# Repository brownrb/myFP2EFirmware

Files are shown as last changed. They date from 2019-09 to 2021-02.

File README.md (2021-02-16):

# myFP2ESP Firmware for ESP32 and ESP8266 myFP2ESP Controllers
This is the firmware for the myFocuserPro2E ESP8266 and ESP32 focus controller projects on Sourceforge.

(c) Robert Brown and Holger Manz, 2019-2021. All rights reserved.

The source code is located in the **src** folder. 

#APPLICATIONS
The Windows applications are found on Sourceforge.  
https://sourceforge.net/projects/myfocuserpro2-esp32/files/Windows%20Application/  

The Linux application and source code is found on Sourceforge.  
https://sourceforge.net/projects/myfocuserpro2-esp32/files/Linux%20Application/  

The ASCOM drivers are found on Sourceforge.  
https://sourceforge.net/projects/myfocuserpro2-esp32/files/ASCOM%20Drivers/  

# FIRMWARE
The firmware is found on GitHub. Download as a zip file then extract the zip file to access the library files and firmware.  
https://github.com/brownrb/myFP2EFirmware/releases

# PCB GERBER FILES  
The Gerbers files for the PCB are found on Sourceforge.  
https://sourceforge.net/projects/myfocuserpro2-esp32/files/PCB%20Gerber%20Files/  

# PDF
To get a clear understanding of myFP2ESP features and options, it is essential to read the PDF.  
https://sourceforge.net/projects/myfocuserpro2-esp32/files/Documentation/  

# Compiling for ESP8266
Compiling the source code requires Arduino IDE **v1.8.13** with the ExpressIF ESP8266 Arduino extensions.
You will need to add the JSON file for the ESP8266 library by using the File->Preferences menu of the 
Arduino IDE and add the location for the library into the board manager
http://arduino.esp8266.com/stable/package_esp8266com_index.json

Once specified, open the board manager, scroll down to ESP8266 and install version **v2.7.4**.
Then you can specify the target board as **Node MCU v1.0 (ESP-12E)** with Flash Size set to 4M (1MB SPIFFS) and upload speed of 115200.

Note: Additional JSON files are separated in board manager by using a comma ,

# Compiling for ESP32
Compiling the source code requires Arduino IDE **v1.8.13** with the ExpressIF ESP32 Arduino extensions.
You will need to add the JSON file for the ESP32 library by using the File->Preferences menu of the 
Arduino IDE and add the location for the library into the board manager
https://dl.espressif.com/dl/package_esp32_index.json  

Once specified, open the board manager, scroll down to ESP32 and install the latest version
Then you can specify the target board as **ESP32 Dev** with Flash Size set t 4M (1MB SPIFFS) and upload speed of 115200.

### Note1:  
Additional JSON files are separated in board manager by using a comma ,  
### Note2:  
When installed the folder C:\Program Files (x86)\Arduino\libraries\WiFi prevents compiling of ESP8266 firmware so move the WIFI folder to C:\Program Files (x86)\Arduino\libraries.old\WiFi  

# Additional JSON library Needed
Make sure you install the library ArduinoJson into the Arduino IDE else firmware will not compile.
The latest version is at https://github.com/bblanchon/ArduinoJson/releases  

# Libraries
To compile you will also need to import these libraries in the folder src/myFP2ELibs into the Arduino IDE environment using the Menu - Sketch - Include Library - Add .Zip file

* myOLED
* myHalfStepperESP32
* myDallasTemperature
* myfp2eIRremoteESP8266

Do not edit or replace any of these library files with others.

# Additional Libraries which must be downloaded and installed
To compile this firmware you need to ensure that you have installed a number of "library" files into the Arduino environment. For each of the links below, you need to DOWNLOAD the ZIP file first.

OneWire
https://github.com/PaulStoffregen/OneWire  

IRRemote
https://github.com/crankyoldgit/IRremoteESP8266  

DuckDNS
https://github.com/ayushsharma82/EasyDDNS  

ESP32 Sketch Data uploader
https://github.com/me-no-dev/arduino-esp32fs-plugin/releases/  

ESP8266 Sketch Data uploader
https://github.com/esp8266/arduino-esp8266fs-plugin  

After downloading the zip files, you then need to install these into the Arduino IDE environment. To do that, start the Arduino IDE, select Sketch, Include Library, Add .Zip library, then navigate to where the ZIP files are stored and select them (you can only load 1 zip file at a time so please repeat this for all ZIP files).

The Sketch Data uploaders require a different method for installing. The install instructions are found in their respective download pages and require copying the files into a special folder of the Arduino program installation.

Once you have done this, you can start programming the controller.

# Hardware Driver Boards
One firmware file supports all driver boards [a different file supports the L293D motor shield driver board for the ESP8266]. The user must set the **DRVBRD** at the beginning of the firmware file [myBoards.h] to the correct driver board, eg, #define DRVBRD PRO2EULN2003 will set the driver board to an ULN2003 using an ESP8266 chip.

# focuserconfig.h
Configuration information about the controller is specified in the *focuserconfig.h* file. This is where you specify the controller options like OLEDTEXT and HOMEPOSITIONSWITCH, as well as the controller mode such as ACCESSPOINT or STATIONMODE.

# Controller Modes
The controller supports the modes ACCESSPOINT, STATIONMODE, LOCALSERIAL for ESP8266 with an additional BLUETOOTHMODE for the ESP32.

# Command Process Handler Routine
At present a single command process handler manages received commands for LOCALSERIAL, BLUETOOTH [ESP32 only] of TCP/IP. This must handle each controller mode, so some variables had to be made global to do this.

# FocuserSetupData.cpp and .h files
At present these must be in the same folder as the .ino file, but will later migrate to a library. These files handle the SPIFFS data, saving, restoring and persistance of controller settings. A JSON file in file system SPIFFS area is used to store focuser data.

# myBoards.cpp and .h files
This implements a driver board class for the supported driver boards [DRV8825, ULN2003, L298N, L293DMINI, L9110S]. There is one constructor for this class which accepts the boardtype, the user should never have to change the main code within the firmware file which sets up the driver boards. All pins mappings for the controller chip, hardware options and the driver board are specified here. DO NOT MODIFY THESE FILES.

# generalDefinitions.h
This file contains general definitions for all controllers, such as motor speed, step modes, focuser limits etc.

# ESPQueue.h
This file manages the Bluetooth serial data for ESP32 chips. It is a modified version of the Queue.h file from Steven de Salas. DO NOT MODIFY THIS FILE. It has been modified to work with ESP8266 and ESP32 chips.

# HalfStepperESP32 Library
This library manages the stepping modes for the ULN2003, L298N, L293DMINI and L9110S driver boards. It is a modified version of the HalfStepper library from Tom Biuso. DO NOT MODIFY THESE FILES. It has been modified to work with ESP8266 and ESP32 chips.

# myOLED Libary
This is a special cut down version of the SSD1306AsciiWire library by Bill Greiman. The library has been reduced in size and a number of additional features added. DO NOT MODIFY THESE FILES.

# COMPILE ENVIRONMENT : Tested with 

* Arduino IDE 1.8.13
* ESP8266 Arduino Core 2.7.4

Libraries 

* Arduino JSON 6.15.2 https://github.com/bblanchon/ArduinoJson.git  
* myfp2eIremoteESP8266 as in Library Files
* myOLED as in Library Files
* myHalfStepperESP32 as in Library Files
* myDallas Temperature as in Library Files
* Wire [as installed with Arduino 1.8.13]
* OneWire http://www.pjrc.com/teensy/td_libs_OneWire.html  

# Notes:
You may need to turn 12V off to reprogram chip. Speed is 115200. Sometimes you might need to
remove the chip from PCB before re-programming new firmware. Remember to remove WIFI library
as instructed in PDF when programming ESP32.

# ESP8266 ISSUES
One chip I have boots fine.
Another chip will not boot properly from 12V only. I need to plug in USB cable, press reset 
then turn on 12V for it to boot correctly. ESP8266 Arduino lib 2.2.0 does not work with this 
chip either.

# TODO
Look at what need to be when chip starts up, do we need a delay reset circuit?

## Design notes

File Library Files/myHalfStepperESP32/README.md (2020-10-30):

# myFP2E Firmware for ESP32 and ESP8266
This is the firmware for the myFocuserPro2E ESP8266 and ESP32 focus controller projecta on Sourceforge.
https://sourceforge.net/projects/arduinoascomfocuserpro2diy/files/myFocuserPro2E/
https://sourceforge.net/projects/myfocuserpro2-esp32/

(c) Robert Brown, 2019. All rights reserved.
(c) Holger Manz, 2019. All rights reserved.

The source code is located in the src folder. 

#HalfStepperESP32.h and HalfStepperESP32.cpp
This file manages the stepping modes for the ULN2003, L298N, L293DMINI and L9110S driver boards. It is a modified version of the HalfStepper library from Tom Biuso. DO NOT MODIFY THESE FILES. It has been modified to work with ESP8266 and ESP32 chips.

# HalfStepper

#### An Arduino library to enable half-stepping and single/dual phasing for step motors.
---

HalfStepper decorates (wraps) the Stepper library to provide half-step states and has options for single/dual phasing as well as multiple coil sequencing options.
<br/>
<br/>This library is able to drive motors directly or through drivers with motor control or H-bridge chips, such as the L293, L298, and L9110.

---

## License
Copyright � 2016 Tom Biuso.
<br />This library is released under the GNU Lesser General Public License v3.0.
<br />See LICENSE file for detailed terms and LGPL v3.0 license text.
<br />
<br />Based upon the Stepper Arduino library.
<br />Copyright � Arduino LLC, Sebastian Gassner, Noah Shibley.
<br />Also released under the GNU LGPL.

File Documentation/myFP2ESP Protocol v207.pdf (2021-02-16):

1 | P a g e

## myFP2ESP Comms Protocol

© Robert Brown, 2014-2021. All Rights Reserved. © Holger Manz, 2019-2021. All Rights Reserved. myFP2™, myFP2ESP8266™, myFP2ESP32™ v207 (17-February-2021)
Applicable to Firmware version 144+

### GENERAL PRINCIPLES

// Command Protocol, commands to controller begin with : and end with #
// responses from controller begin with Char, then response and end with #
// the char response indicates what command requested the response, ie. P = Get focuser Position

// Not all commands return responses

### COMPATIBILITY WITH MYFOCUSERPRO2 IN LOCALSERIALMODE

In general, when configured as LOCALSERIAL, myFP2 applications and drivers should be able to be control the myFP2ESP controller.

### INDI

In general, the myFP2ESP controller will work with the existing INDI driver for myFP2 either in Serial USB or TCP/IP modes.

2 | P a g e

### COMMANDS [TCP/IP OR SERIAL OR BLUETOOTH]

:00# | Pxxxx# | Get current focuser position
:01# | Ixx# | Get motor moving status - 1 if moving, 0 otherwise
:02# | EOK# | Get motor controller status - Controller Response to "Are we connected"
:03# | F204# | Get Controller firmware version string (Fxxx#)
:04# | FString# | Get firmware version string (Fprogram name, version, #)
:05xxxxxx# | None | Set new target position to XXXXXX
| | (and focuser initiates immediate move to XXXXXX)
:06# | Zxxxxxx# | Get temperature as a float xx.xx
:07xxxxxx# | None | Set MaxStep between 1000 and 2000000
:08# | Mxxxxxx# | Get MaxStep, returns Long Integer XXXXXX
:09# | | Not used
:10# | Yxxxxxx# | Get MaxIncrement, returns maxsteps value XXXXXX
:11# | Oxx# | Get Coil Power setting
| | (0 = coils released after move, 1 = coil pwr on after move)
:12xx# | None | Set Coil Power 0=release pwr after move, 1=keep power on after move
:13# | Rxx# | Get Reverse Direction setting, 0 off, 1 on
:14xx# | None | Set Reverse Direction setting 0=normal, 1=reversed
:15xx# | None | Set Motor speed, 0 = Slow, 1 = Med, 2 = Fast
:16# | None | Display in Celsius (LCD or TFT)
:17# | None | Display in Fahrenheit (LCD or TFT)
:180# | None | Set the return of user specified stepsize to be OFF - default
:181# | None | Set the return of user specified stepsize to be ON
:19xxxx# | None | Set the step size value - double type, eg 2.1 (0.001-50.0)
:20xx# | None | Set the temperature resolution setting for DS18B20 temperature probe
:21# | Qxx# | Get temperature probe resolution setting (9, 10, 11 or 12)
:22xxx# | None | Set the temperature coefficient value to xxx
:23x# | None | Set the temperature compensation ON (1) or OFF (0)
:24# | 1xx# | Get state of Temperature Compensation, 0=disabled, 1=enabled
:25# | Ax# | Get if Temperature Compensation available 0=No, 1=Yes
:26# | Bxxx# | Get Temperature Coefficient (in steps per degree)
:27# | None | Stop a move - like a Halt
:28# | None | Home the motor to position 0
:29# | Sxx# | Get stepmode, returns XX
:30xx# | None | Set stepmode
(1=Full, 2=Half, 4=1/4, 8=1/8, 16=1/16, 32=1/32, 64=1/64, 128=1/128, 256=1/256)
:31xxxxxx# | None | Set current motor position to XXXXXX
| | (does not move, updates currentpos and targetpos to XXXXXX)
:32# | Ux# | Get if Stepsize is enabled in controller (true or false, 0/1)
:33# | Txxxxx# | Get step size in microns (if enabled by controller)
:34# | Xxxxxx# | Get the time that an LCD screen is displayed for
| | (in milliseconds, eg 2 = 2seconds
:35xxxx# | None | Set length of time an LCD page is displayed for in seconds 2-10s
:360# | None | Disable Display
:361# | None | Enable Display
:37# | Dxx# | Get Display status 0=disabled, 1=enabled
:38# | b# | Get Temperature Mode, Celsius=1, Fahrenheit=0
:39# | Nxxxxxx# | Get the new motor position (target) XXXXXX (not used yet)
:40# | None | Reboot controller
:41# | String# | Troubleshooting only

3 | P a g e
:42# | None | Reset focuser defaults
:43# | Cx# | Get motorspeed (0=slow, 1=medium, 2=fast)
:44xxx# | None | RETIRED from firmware 292 onwards
| | (set motorspeed threshold when moving)
:45# | Gxxx# | RETIRED from firmware 292 onwards (get TSWTHRESHOLD - 200)
:46x# | None | RETIRED from firmware 292 onwards
| | (set enable/disable motorspeed change when moving)
:47# | Jx# | RETIRED from firmware 292 onwards
| | (get state of motorspeedchange, enabled/disabled)
:48# | None | Save settings in SPIFFS
:49# | aString# | Get authenticated firmware MD5 Hash
:50# | lx# | Get if Home Position Switch enabled in firmware, 0 = no, 1 = yes
:51# | dipaddr# | Get ESP-WiFiController IP Address
:52# | enum# | Get ESP-WiFiController number of TCP packets sent
:53# | fnum# | Get ESP-WiFiController number of TCP packets received
:54# | gstr# | Get ESP-WiFiController SSID
:55# | 0xxxx# | Get motor speed delay (for current speed setting)
:56xxxx# | None | Set motor speed delay (for current speed setting)
:57# | None | Set Super Slow Jogging Speed [0 or 1]
:58# | mxxxx# | get Features [now redundant]
:59# | | Unused
:60xx# | None | Set MotorSpeed when jogging
:61xx# | None | Set update of position on lcd when moving (0=disable, 1=enable)
:62# | Lxx# | Get update of position on lcd when moving (0=disable, 1=enable)
:63# | Hxx# | Get status of home position switch (0=off, 1=closed, position 0)
:64xxx# | None | Move a specified number of steps (relative mode + or -)
:65x# | None | Set jogging state enable/disable
:66# | Kxx | Get jogging state enabled/disabled
:67x# | None | Set jogging direction, 0=IN, 1=OUT
:68# | Vx# | Get jogging direction, 0=IN, 1=OUT
:69# | None | RETIRED (sets EEPROMWRITES to 0)
:70# | Wxxxxxx# | RETIRED (gets number of EEPROMWrites so far, Nano up to 10,000)
:71xxx# | None | Set DelayAfterMove
:72# | 3xxx# | Get DelayAfterMove
:730# | None | Disable backlash IN (going to lower focuser position)
:731# | None | Enable backlash IN
:74# | 4x# | Get backlash IN enabled status [0 or 1]
:750# | None | Disable backlash OUT (going to higher focuser position)
:751# | None | Enable backlash OUT
:76# | 5x# | Get backlash OUT enabled status [0 or 1]
:77xx# | None | Set backlash steps IN
:78# | 6xx# | Get number of backlash steps IN
:79xx# | None | Set backlash steps OUT
:80# | 7xx# | Get number of backlash steps OUT
:81# | 8xxx# | Get number of backlash maximum steps
:82xxx# | None | Set backlash maximum steps
:83# | cx# | Get if there is a temperature probe, 0 = No, 1 = Yes
:84# | None | Set Nextion Page
:85xxx# | None | Set Serial Port Speed [Nextion only], xxx=9600, 19200, 38400, 57600
:86# | jxxxx# | Get Serial Port Speed [Nextion only]
:87# | kx# | Get Temperature compensation direction (1=IN, 0 =OUT)

4 | P a g e
:88x# | None | Set Temperature compensation direction (1=IN, 0 =OUT)
:89x# | 9x# | Get stepper power [myFP2]
:90xyyyy# | None | Set preset x [0-9] with position value yyyy [unsigned long]
:91x# | hyyyyy# | Get preset number x [0-9] [as unsigned long]
:92xxx# | None | Set OLED page display option
:93# | lxxx# | Get OLED page display option
:94x# | | Set DelayedDisplayUpdate (0=disabled, 1-enabled)
:95# | nx# | Get DelayedDisplayUpdate (0=disabled, 1-enabled)
:96x# | None | Set management options
| | (ASCOM server=1, in-out leds=2, temp probe=4, webserver=8)
:97# | mx# | Get management options
| | (ASCOM server=1, in-out leds=2, temp probe=4, webserver=8)
:98# | sx# | Get Network Signal Strength RSSI
:99x# | | Set Home Position Switch state [0=disabled, 1-enabled]

RETURNED VALUES BEGIN WITH A CHAR, FOLLOWED BY A VALUE (AS A STRING) AND TERMINATED WITH A HASH #

5 | P a g e

### MANAGEMENT SERVER [PORT 6060]

FILE MANAGEMENT
/delete | Delete a SPIFFS file
/list | List all SPIFFS files
/upload | Upload a file to SPIFFS

ASCOM REMOTE ALPACA SERVER
/ascomoff
/ascomon

IN-OUT LED’s
/ledsoff
/ledson

TEMPERATURE PROBE
/tempon
/tempoff

WEB-SERVER
/webserveroff
/webserveron

CONTROLLER OPTIONS
/halt | Halt the focuser motor [if moving]
/reboot | Reboot the myFP2ESP controller

NETWORK OPTIONS
/rssi | Return Network Signal Strength

6 | P a g e

### JSON CALLS

/set? | Set specific service or value
/set?ascom=off | Stop the ASCOM Alpaca remote server
/set?ascom=on | Start the ASCOM Alpaca remote server
/set?coilpower=off | Disable Coil power
/set?coilpower=on | Enable Coil power
/set?display=off | Disable the OLED display
/set?display=on | Enable the OLED display
/set?hpsw=off | Disable Home Position Switch
/set?hpsw=on | Enable Home Position Switch
/set?leds=off | Disable the IN-OUT LED’s
/set?leds=on | Enable the IN-OUT LED’s
/set?motorspeed=0 | Set Motor speed [0=slow, 1=medium, 2=fast]
/set?move=4192 | Move the focuser to position 4192
/set?position=5000 | Set focuser position to 5000 [Not a move]
/set?reverse=off | Set Reverse Direction off
/set?reverse=on | Set Reverse Direction on
/set?tempprobe=on | Enable the temperature probe [if fitted]
/set?tempprobe=off | Disable the temperature probe [if fitted]
/set?webserver=off | Stop the web-server
/set?webserver=on | Start the web-server
/get? | Get specific service or value
/get?ascom= | Return state of ASCOM Alpaca Remote Server [0 = off/disabled,
1=on/enabled]
/get?coilpower= | Return state of Coil power
/get?display= | Return state of display
/get?leds= | Return state of IN-OUT LED’s
/get?hpsw= | Return state of Home Position Switch [0=disabled, 1=enabled]
/get?ismoving= | Return if focuser is moving
/get?motorspeed= | Return motorspeed [0=slow, 1=medium, 2=fast]
/get?position= | Return the focuser position
/get?reverse= | Return reverse direction [0 = off/disabled, 1=on/enabled]
/get?tempprobe= | Return state of temperature probe
/get?webserver= | Return state of web-server
/get?rssi= | Return network strength

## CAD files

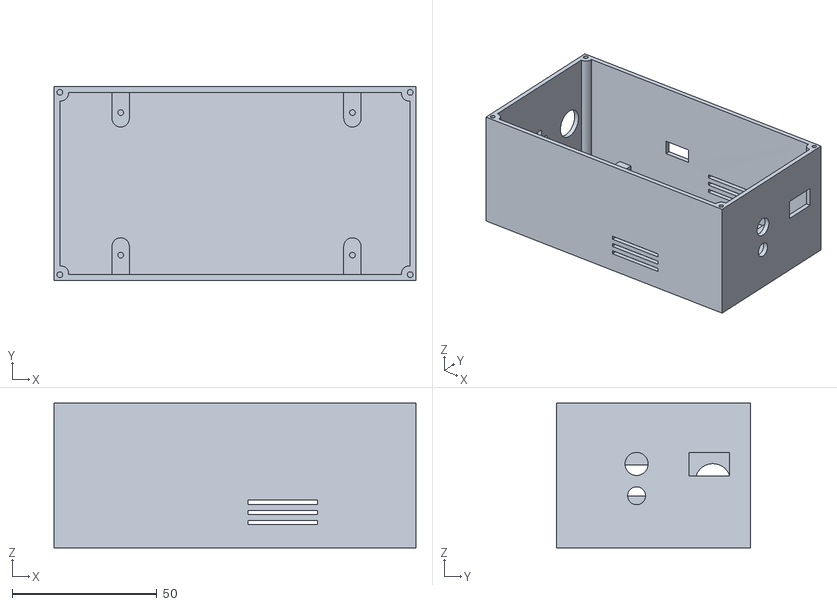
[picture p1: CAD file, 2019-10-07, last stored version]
3D Printed Cases/ESP32/DRV8825/Case-ESP32-DRV-PB-OLED-00.stl
125.0 x 67.0 x 50.0

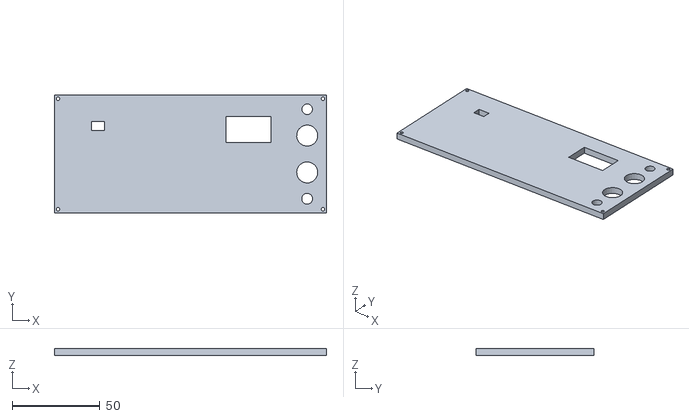
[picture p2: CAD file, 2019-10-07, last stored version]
3D Printed Cases/ESP32/ULN2003/Lid-ESP32-ULN-PB-OLED-IR-00.stl
155.0 x 67.0 x 4.00

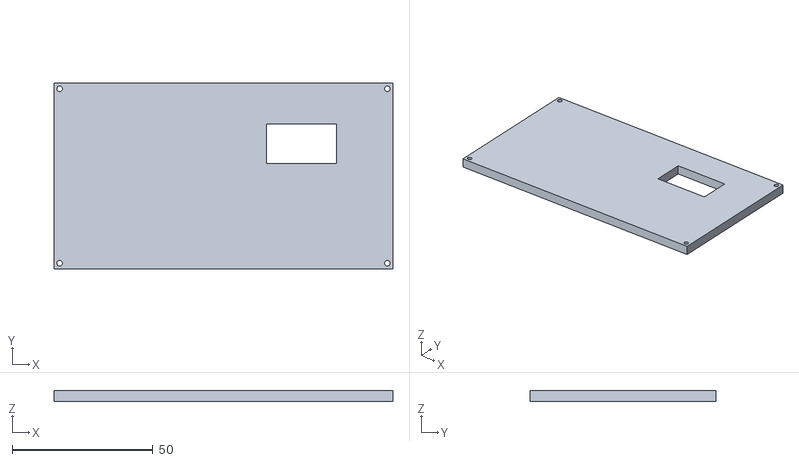
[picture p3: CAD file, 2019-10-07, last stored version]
3D Printed Cases/ESP8266/DRV8825-Big Chip/Lid-OLED-B-DRV-NoHoles-00.stl
120.5 x 66.0 x 4.00

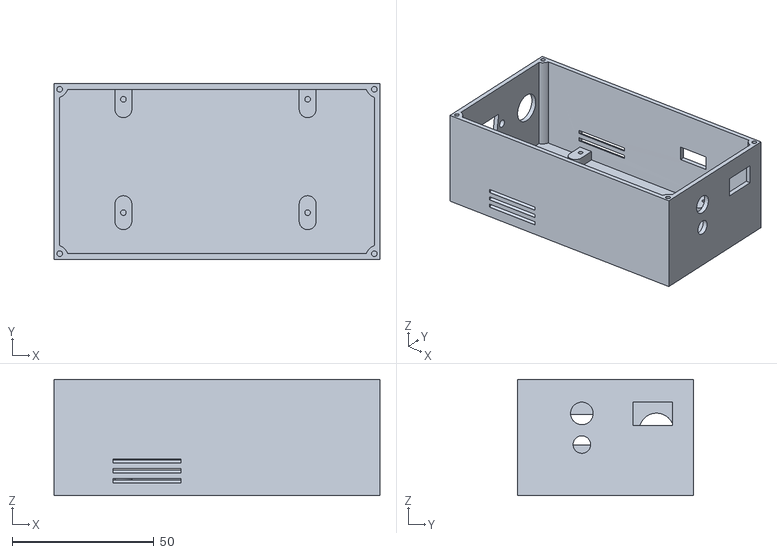
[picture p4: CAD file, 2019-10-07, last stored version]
3D Printed Cases/ESP8266/DRV8825/Case-S-DRV-00.stl
115.0 x 62.0 x 41.0

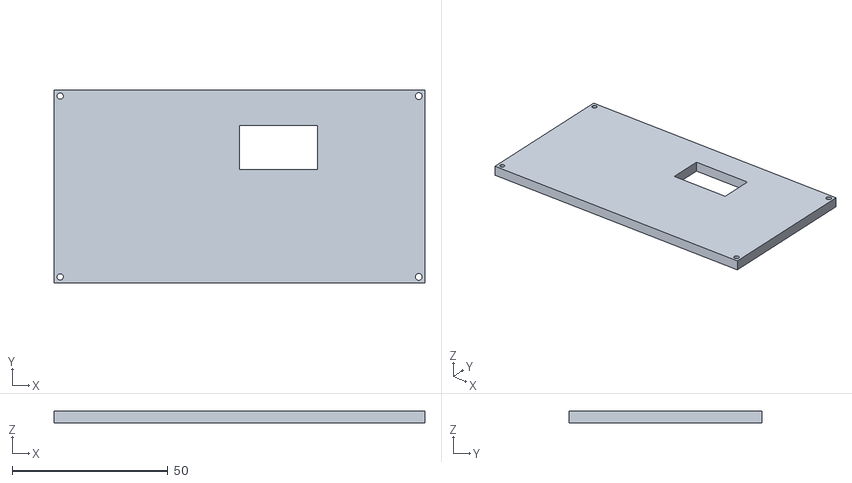
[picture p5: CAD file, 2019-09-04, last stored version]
3D Printed Cases/ESP8266/L293D Motor Shield/Lid-OLED-L293D-Shield-NoHoles-00.stl
119.0 x 62.0 x 4.00

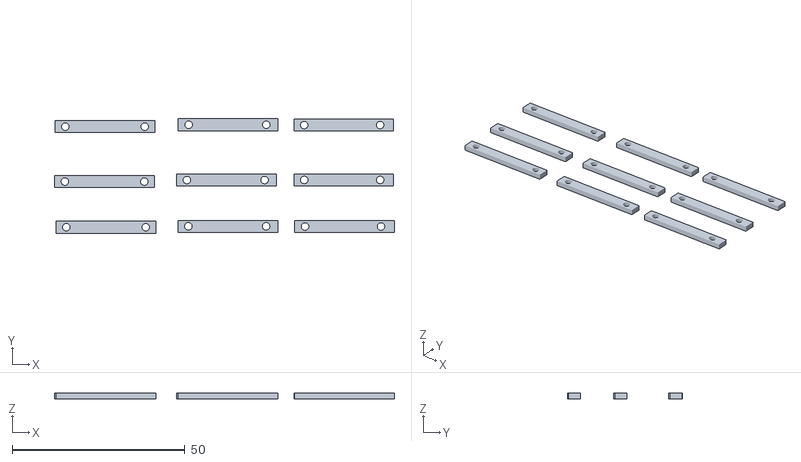
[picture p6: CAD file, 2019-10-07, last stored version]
3D Printed Cases/ESP8266/Lid OLED Little Spacer/lid-oled-support-22-23mm.stl
98.5 x 33.2 x 1.60

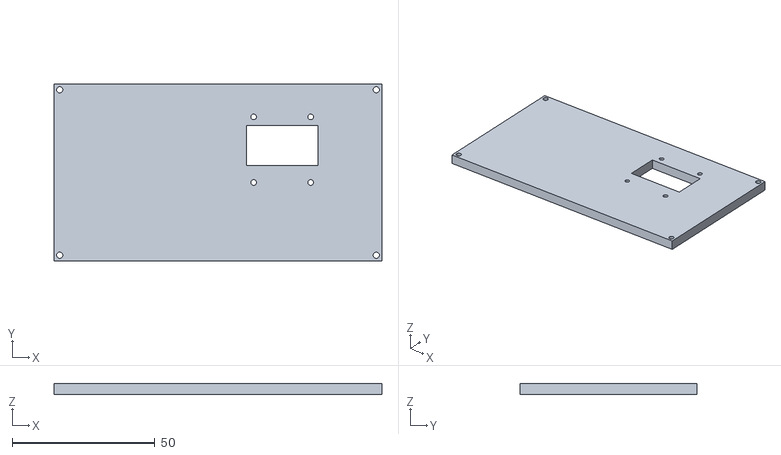
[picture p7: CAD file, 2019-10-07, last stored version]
3D Printed Cases/ESP8266/Lid-OLED-Shenglongsi-00.stl
115.0 x 62.0 x 4.00

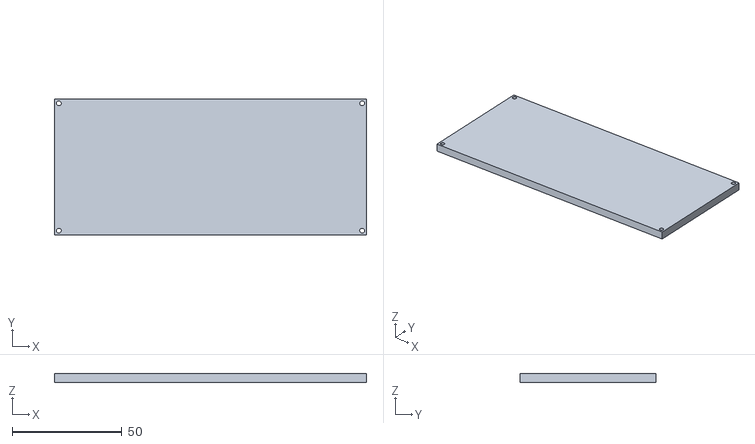
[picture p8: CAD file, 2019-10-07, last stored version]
3D Printed Cases/ESP8266/ULN2003-L298N/Lid-ULN-L298N-NOLED-00.stl
142.0 x 62.0 x 4.00

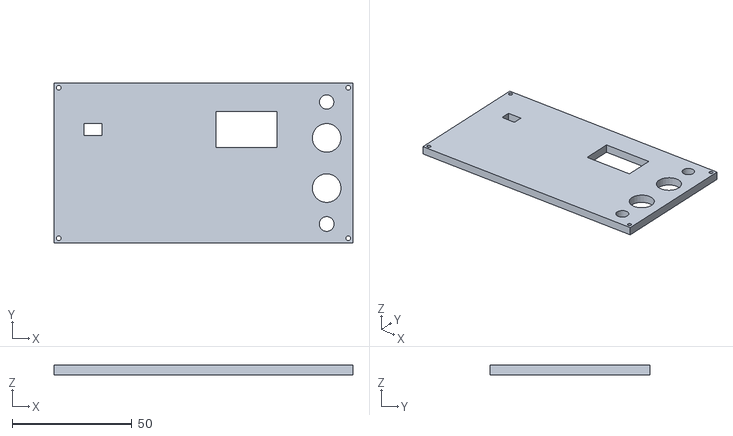
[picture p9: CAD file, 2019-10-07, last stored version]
3D Printed Cases/ESP32/DRV8825/Lid-ESP32-DRV-PB-OLED-IR-00.stl
125.0 x 67.0 x 4.00

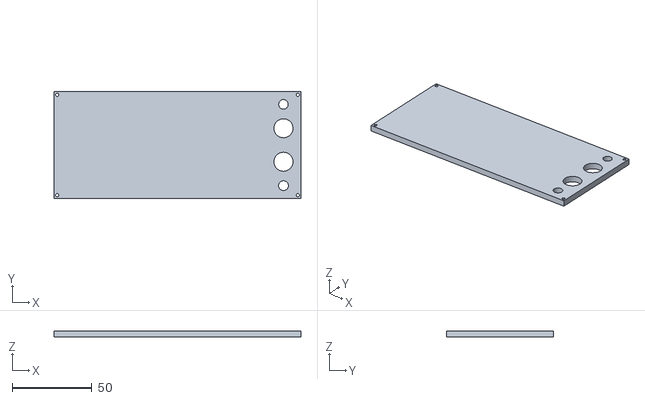
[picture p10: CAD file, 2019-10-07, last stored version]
3D Printed Cases/ESP32/ULN2003/Lid-ESP32-ULN-PB-00.stl
155.0 x 67.0 x 4.00

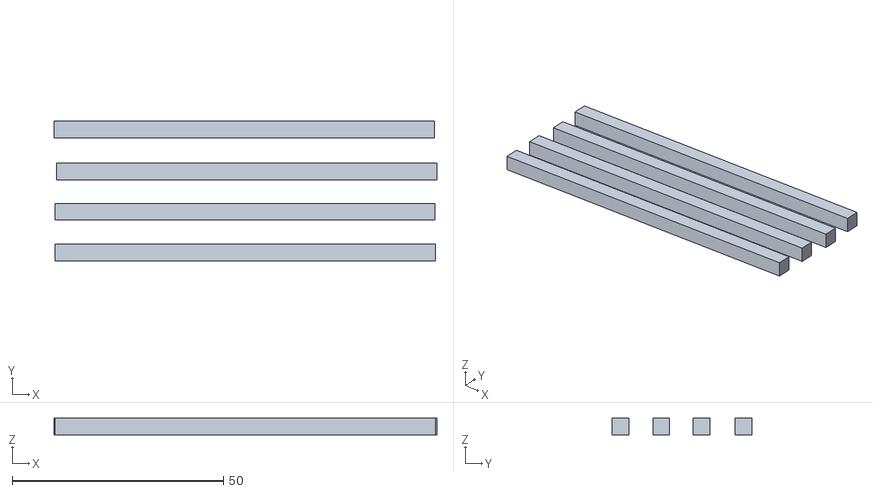
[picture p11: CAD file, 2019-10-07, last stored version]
3D Printed Cases/ESP8266/Bracing for E-oled lid.stl
90.6 x 33.1 x 4.00

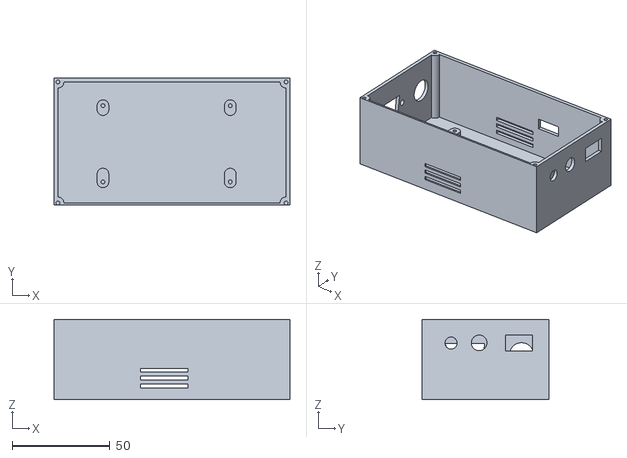
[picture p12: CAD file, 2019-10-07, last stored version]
3D Printed Cases/ESP8266/DRV8825-Big Chip/Case-B-DRV-00.stl
120.5 x 64.8 x 41.0

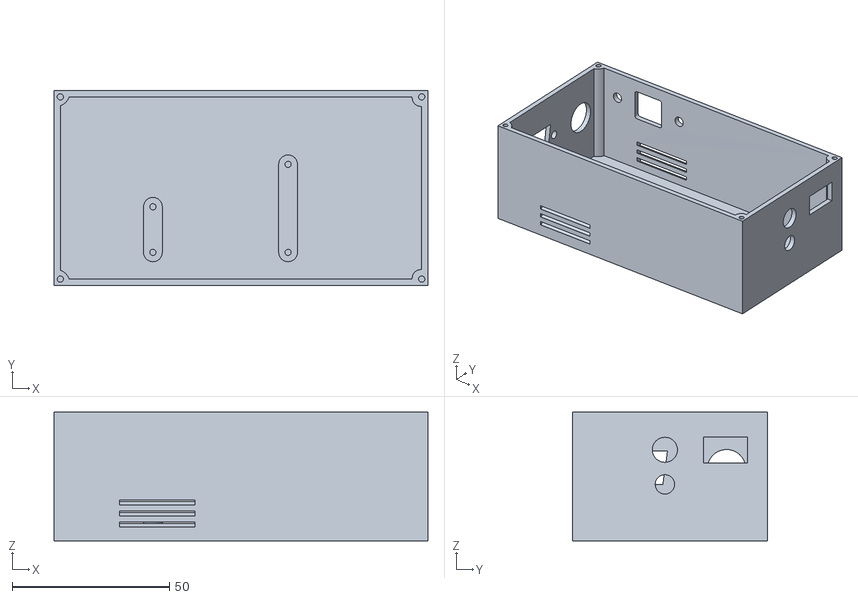
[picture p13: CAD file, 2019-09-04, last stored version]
3D Printed Cases/ESP8266/L293D Motor Shield/Case-L293D-Shield-00.stl
119.0 x 62.0 x 41.0

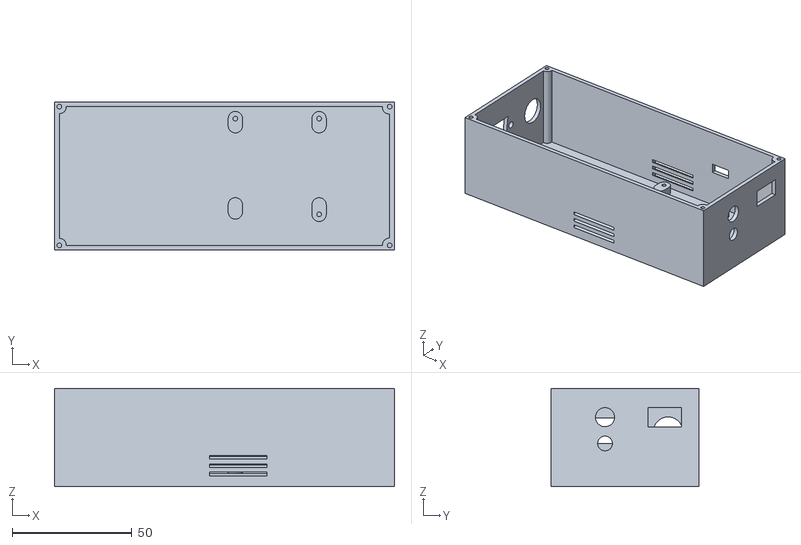
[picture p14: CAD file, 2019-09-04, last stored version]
3D Printed Cases/ESP8266/ULN2003-L298N/Case-ULN-L298N-00.stl
142.0 x 62.0 x 41.0

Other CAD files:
3D Printed Cases/ESP8266/ULN2003/Case-ULN-00.stl
src/PCB gerbers/3D-Lid-ESP8266-ULN-L298N-OLED-00.stl
3D Printed Cases/ESP32/DRV8825/Lid-ESP32-DRV-00.stl
3D Printed Cases/ESP32/DRV8825/Lid-ESP32-DRV-OLED-00.stl
3D Printed Cases/ESP32/DRV8825/Lid-ESP32-DRV-PB-00.stl
3D Printed Cases/ESP32/DRV8825/Lid-ESP32-DRV-PB-OLED-00.stl
3D Printed Cases/ESP32/ULN2003/Case-ESP32-ULN-00.stl
3D Printed Cases/ESP32/ULN2003/Lid-ESP32-ULN-00.stl
3D Printed Cases/ESP32/ULN2003/Lid-ESP32-ULN-OLED-00.stl
3D Printed Cases/ESP32/ULN2003/Lid-ESP32-ULN-PB-OLED-00.stl
3D Printed Cases/ESP8266/Lid-00.stl
3D Printed Cases/ESP8266/Lid-OLED-00.stl
3D Printed Cases/ESP8266/Lid-OLED-NoHoles-00.stl
3D Printed Cases/ESP8266/ULN2003-L298N/Lid-ULN-L298N-OLED-00.stl
src/PCB gerbers/3D-Lid-ESP8266-ULN-00.stl
src/PCB gerbers/3D-Lid-ESP9266-ULN-OLED-NoHoles-00.stl
src/PCB gerbers/3D=Case-ESP8266-ULN-00.stl

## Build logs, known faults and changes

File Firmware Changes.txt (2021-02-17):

147
Add WEMOSDRV8825H (Holger) to myBoards.h/.cpp and myBoardTypes.h

146
Fix for a number of compiler warnings
Fix for missing brackets in line 1141 in myFP2ESP.ino

145
Move HOMEPOSITIONSWITCH to Management Server

144
Fix for RSSI

143
Add rssi calls to comms.h and management server and webserver interfaces

142
managementserver.cpp - line 985 change to DELETE LINE Serial.print
Add stepmode up to 256 for future support of Trimac steppers
Rename temprecision to tempresolution
Disable TIMEDTESTS in generalDefinitions.h
Fix error of reboot cause by Enabling/Disabling temperature probe

141
Change driverboard->halt() - no need to return stepcount
Fix for using Serial.print commands in MachineStateBacklash - changed to DebugPrint
Fix for 2nd network credential not being updated [readwificonifg() ]
Fix for Home Position Switch not working in Backlash

140
Fix IR_HALT compile error if IRREMOTE is enabled
Fix MDNS compile errors if MDNSSERVER is enabled
Fix for Backlash
Fix for oledtextmsg compile issues when OLED_TEXT enabled
Change stepmode to int type (mySetupData and DriverBoard) to allow Trimac drivers in a future release
Add generic get/set interface calls
Add additional comms calls
Add comms calls to support myFocuserPro2 INDI driver
Add MotorSpeedDelay web page and comms calls
Allow INDI to be used over TCP/IP as well as Serial
Add additional WiFi logon credentials as a fallback
Add additional calls on webserver, temp, position, ismoving,
Fix for webserver not restarting

130
Fix for print(F()) errors
Fix for OLEDTEXT compile error
Fix for Focuser position not being updated on display when moving
Fix for HalfStepperESP32 amd mystepper library code - must reinstall
Fix for fcurrentPosition compilation errors in some options
Fix for PRO2EL293D28BYJ48 and PRO2EL293DNEMA to use myStepper library
Fix error in update_irremote() for focuser position
Fix compilation error for station mode in setup() re OLEDGRAPHICS
Fix error in ASCOM SERVER root page
Add temperature XHTML update to webserver home page wsindex.html
Add HPSW messages to generaldefinitions.h/.cpp
Completed test for all driver boards L9110S, L293D, ULN2003, L293DMINI, L298N, DRV8825

126
Rewrite web/management/ascom-remote server send page routines
Move focuserposition to driverboard.cpp, simplifies a lot of code
Implement timing statements for some code functions [to support debugging and optimization]
Implement HTTP_GET functions for most web/management/ascom server pages
Optimize web/management server code
Optimize html files and code handling routines for Webserver and Management server
Use Timer interrupts to move motor
Use common speed setting MSPEED for each driverboard
Remove speed settings in driverboard
Remove references to driverboard->setmotorspeed
Remove IRREMOTE from ESP8266 as those boards do not have support for IRREMOTE on PCB
Remove joystick speed code - now redundant 
Add ability to change temp between C/F on management web server page
Add webserver and management server page fonts/colors/layout
Add additional management web server page into 4 pages
Add management server page2 to display services to ENABLE/DISABLE WEBSERVER/ASCOMREMOTESERVER/TEMPERATUREPROBE
   and IN-OUT LEDS
Add management server page3 to display backlash settings
Add management server page4 to customize web page colors
Add management server page5 to display webpicker
Add SHOWSTARTMESSAGE to management webserver and remove define from focuserconfig.h
Add SHOWHPSWMESSAGES to management webserver and remove define from focuserconfig.h
Add MANAGEMENTFORCEDOWNLOAD to management webserver and remove define from focuserconfig.h
Add INOUTLEDS to management webserver and remove define from focuserconfig.h
Add BACKLASH to management webserver and remove define from focuserconfig.h
Add TEMPERATUREPROBE to management webserver and remove define from focuserconfig.h
Add WEBSERVER to management webserver and remove define from focuserconfig.h
Add ASCOMREMOTESERVER to management webserver and remove define from focuserconfig.h
Add SaveNow() into focuserSetupData so settings are saved immediately before rebooting
Add debug statements for printing available HEAP memory to aid debugging
Fix for motorspeed setting when using joystick or infrared remote - esp32drv8825
Fix for presets not being saved
Fix for FocuserSetupData.cpp - ESP8266 - check if file exists BEFORE attempting to delete it [avoid potential crash]
Fis for FocuserSetupData.cpp - ESP8266 - issues related to file access [avoid potential crash]
Fix for Presets on webserver presets page
Fix bug in debug statement for mdnsserver
Fix for OLED text on Management and Web server pages
Fix for display of temperature on Web Server pages
Fix for low heap memory - release web/management/ascom server strings after sending pages
Fix for low heap memory - only build strings for web/management/ascom server pages as required
Rewrite myBoards.cpp driverboard initialization code
Implement myfp2eIRemoteESP8266 library to handle IRREMOTE to reduce space footprint
Fix for focuser moving to 0 on reload
Fix for random reboots related to focusersetupdata.cpp
Fix for IRRemote key mapping for "5"
Change webserver index page to reload target position at regular intervals

122
Fix for OLED text on Management and Web server pages
Fix for display of temperature on Web Server pages
Add ability to change temp between C/F on management web server page
Presets fix
Fix for listspiffsfiles

r121
Fix issue with Home Position Switch

r120
Fix issue with tcpserver on esp8266 [port cannot be changed dynamically]
reverse direction fix (and home position switch now obeys it to)

r119
Add alpacadiscovery protocol support (UDP port 32227, IPv4)
Move ASCOMGUID into ascom definitions rather than hard coded
Fix setfeatures
Fix stepmode
On Webserver - Add ability to change TCP/IP port
Add TCP/IP port to LCD display
Fix code in management server to check for updated port numbers that change
Increase SPIFF file size for data_per.jsn

r118
Display temperature on OLED and Webserver according to tempmode state (C or F)
Add Display Enable/Disable to management console and  Web-server
Change Web-server default refresh rate to 60s [now using dynamic page update]
Reduce number of strings used in Management server and  Web-server
Add IP/DRVBRD info to Move webpage to make consistent with other web pages
Fix port number in webserver notfound page
Convert dynamic web page constants to strings into generaldefinitions.h
Add file upload to SPIFFs into management server

r117
Update copyright notice to include year 2020
When rebooting, check for MDNS and free resources
Fix code in display_oledtext_page2 to display correct port numbers for web/ascom servers
Add READWIFICONFIG as a focuser-config parameter - will read SSID and PASSWORD from wificonfig.json file
Add change port number for mDNS server to management console
Add Start and Stop mDNS server to management console
Check if service is running before attempting to stop service
Add check if MANAGEMENT server is defined without ACCESSPOINT or STATIONMODE defined
Improve layout of management console and web server pages to reduce code overhead
Move focuser presets on webpage to /presets page
Add link on main webpage to presets page
remove un-needed CRLF and spaces from data/*.html pages
Add dynamic web page update to  Web-server /move page xhttp
Add HALT to  Web-server /move page
Add focuser position and ismoving to presets webpage, add dynamic web page update xhhtp
Add ismoving dynamic update to  Web-server home page xhttp
Add halt button and move button to focuser presets web page
Add presets button to move web page
Delete move buttons from main web server page (they are on /move)
Add support for OLED 1.3" displays using SSH1106 driver chip to OLEDTEXT
Add support for OLED 1.3" displays using SSH1106 driver chip to OLEDGRAPHICS
Fix check for OLED display types and driver types
Fix issue with OLED not working on PRO2ESP32R3WEMOS board

116
Add ~finalizer for myBoards class
Fix logic error in Management server list files for ESP8266
Add DebugPrint when starting WiFi.begin()
Add DebugPrint to print error message of SPIFFS.begin() fails
Change temperature/oled update checks to use TimeCheck()
Release memory for servers ( Web-server and ascomserver) if they are stopped
Fix ESP8266 errors in defining  Web-servers and include files
Shorten some names used in SPIFFS file for data_per.jsn
Fix error in starting ascomremoteserver for ESP8266
Add reboot controller button in Management Console
Change all defined strings to uppercase and remove unused strings
Refine Debug and Trace statements in management and web server code
For OLEDTEXT, add detection for I2C display presence
For OLEDTEXT, add checks in routine for displayfound == true

115
Add duckdns mdns otaupdate etc to management page msindex.html
Fix duckdns incorrect define and checks in focuserconfig.h
Add duckdnsstate to main .ino
Rename otaserverstate to otaupdatestate
Add code in management server to handle duckdns state
Add refreshrate for webpages into management console
Add /move page to  Web-server
Add range check for focuser position and presets on  Web-server
Add range check for focuser position and maxsteps on ascom server setup
Improve speed of management and  Web-server pages
Fix issue with IRREMOTE - change to new library
Fix issue with JOYSTICK when moving and release of coil power
In State_Idle, when parking, enforce rule of releasemotor only if coilpower is false
Add TRACE macro
Increase data_per.jsn size to 1023

114
Fix LOCALSERIAL issue
Add INDI config so can work in LOCALSERIAL with INDI
Fix local serial issues line to serialline
Fix for serial.begin() ifdef LOCALSERIAL
Fix for using localserial with INDI serial driver for myFocuserPro2
Fix case 64: comms.h for check focuser position against maxstep
Fix readtemp to read_temp in graphics oled and ascom server temp routines
Change debugprint recstr in comms.h
Fix define for oledgraphics in focuserconfig.h
Implement static pages for ascom server in SPIFFS
Add code to handle new static pages in ascom server
Make small changes to header portions of all server html pages

113
Fix Bluetooth running on WEMOS ESP32
Fix LOCALSERIAL compilation errors
Move  Web-serverPORT to SPIFFS and allow MANAGEMENT SERVER to change the  Web-server port

112
Add management interface on port 6060

111
Fix temperature precision being set on boot
Move code inline
Build web pages in SPIFFS, add dynamic processor
Improve joystick code
Add calibration of joystick to pdf
Create joystick calibation and test programs in Test-programs folder

110
Add focuser presets [0-9] to use with software or infrared remote controller - stored in SPIFFS
Add options for a different joystick (2-Axis PS2 Arduino style)
Restore motorspeed before move [in case joystick has changed the speed]. 
ascomserver, comms, infraredremote, joystick,  Web-server

109
Add ASCOM REMOTE ALPACA Management interface

108
Add 2-axis joystick 
Add joystick to list of controller features

107
Allow mDNS service for most controller modes, change to port 8080

106
For revision 4 ESP32 boards, add HOME POSITION SWITCH
Add mDNS for STATIONMODE/ Web-server
For revision 4 ESP32 boards, add HOME POSITION SWITCH to PCB
Add define for HOMEPOSITIONSWITCH
Add definitions into generalDefinitions.h and myBoards.h for HPSW
Add code to handle HPSW into myFP2ESP.ino

105 04 November 2019
Add ASCOM Alpaca REMOTE support
code reduction/speed improvement in comms
separation of ascomserver, comms, display, temperature,  Web-server definitions and code into separate files

104 02 November 2019
Improve  Web-server support
 Web-server: add halt button to  Web-server
 Web-server: add setpos and gotopos buttons for position
 Web-server: fix bug for value of focuser position when updated
 Web-server: add board information and copyright
 Web-server: fix bug in motorspeed
 Web-server: add define for refresh rate of page
bracket ConnectionStatus in loop() if using ascom remote or  Web-server
add requirement to have either ACCESSPOINT or STATIONMODE defined
add requirement to have either ACCESSPOINT or STATIONMODE or BLUETOOTHMODE or LOCALSERIAL defined
implement controller features: Case 58: Get controller features
fix case 54 to return correct value for SSID when running in different modes
fix error in stepmode for PRO2ESP32DRV8825
fix setstepperspeed in DriverBoard constructor for PRO2EULN2003
fix error in oled display I2C begin, use DRVBRD == instead of defined()
improve stepper motor speed on  Web-server
fix error in case 30 as there is potential issue
oleltext: Change displaypage2 to show controller mode being used
esp_comms() now disabled if using ascom remote or  Web-server

103
Add  Web-server

102
Add PRO2ESP32R3WEMOS
Running ok on ESP32, have wired 470uf to VIN/GND and adjusted current
Add IR Mappings file
Add OTA (over the air updates)
Add LOCALSERIAL (may not work yet on all boards - does not work on L293D ESP8266 Motor Shield)
Fix display enabled bug
Remove EEPROM support, now always SPIFF
Remove motorspeedchange and motorspeedthreshold code
Add stub cases in ESP_Communication() for myFocuserPro2 support when in LOCALSERIAL mode
Extract resource strings in generalDefinitions.h file

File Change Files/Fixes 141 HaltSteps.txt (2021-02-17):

add alternative wifi network credentials

remove halt steps - no longer needed

myFP2ESP.ino
1651
          int haltsteps = driverboard->halt();            // halt returns stepcount
	  // we no longer etc
change to
          driverboard->halt();                            // halt stepper motor

myBoards.h
212 Change to
    void      halt(void);

myBoards.cpp
501
void DriverBoard::halt(void)
{
#if defined(ESP8266)
  myfp2Timer.detachInterrupt();
#else
  timerAlarmDisable(myfp2timer);      // stop alarm
  timerDetachInterrupt(myfp2timer);   // detach interrupt
  timerEnd(myfp2timer);               // end timer
#endif
  DebugPrint(F(">halt_alert "));
  delay(10);
}

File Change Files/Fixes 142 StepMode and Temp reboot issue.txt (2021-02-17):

managementserver.cpp
line 985 change to DELETE LINE Serial.print

// ----------------------------------------------------------------------------------------------
generalDefinitions.h
111
#ifndef STEP64
#define STEP64                64
#endif
#ifndef STEP128
#define STEP128               128
#endif
#ifndef STEP256
#define STEP256               256
#endif

Line 393
change to //#define TIMEDTESTS 1

// ----------------------------------------------------------------------------------------------
ascom.cpp
extern float lasttemp;

delete  extern TempProbe *myTempProbe;

647
  // (1=Full, 2=Half, 4=1/4, 8=1/8, 16=1/16, 32=1/32, 64=1/64, 128=1/128, 256=1/256)
  String fsm_str = ascomserver->arg("sm");
  if ( fsm_str != "" )
  {
    int temp1 = 0;
    DebugPrint("root() -stepmode:");
    DebugPrintln(fsm_str);
    temp1 = fsm_str.toInt();
    if ( temp1 < STEP1 )
    {
      temp1 = STEP1;
    }
    if ( temp1 > STEP256 )
    {
      temp1 = STEP256;
    }
    mySetupData->set_stepmode(temp1);
  }

934
  jsonretstr = "{\"Value\":" + String(lasttemp, 2) + "," + ASCOM_addclientinfo( jsonretstr );

// ----------------------------------------------------------------------------------------------
managementserver.cpp
extern int tprobe1;
1263
  value = mserver.arg("starttp");
  if ( msg != "" )
  {
    // check if already enabled
    if (mySetupData->get_temperatureprobestate() == 1)                // if probe is enabled
    {
      if( tprobe1 == 0 )                                              // if probe not found
      {
        myTempProbe = new TempProbe;                                  // attempt to start probe and search for probe
      }
    }
    else
    {
      mySetupData->set_temperatureprobestate(1);                      // enable probe
      if( tprobe1 == 0 )                                              // if probe not found
      {
        myTempProbe = new TempProbe;                                  // attempt to start probe and search for probe
      }
    }
  }
  msg = mserver.arg("stoptp");
  if ( msg != "" )
  {
    if ( mySetupData->get_temperatureprobestate() == 1 )
    {
      // there is no destructor call
      tprobe1 = 0;
      mySetupData->set_temperatureprobestate(0);
    }
    else
    {
      // do nothing, already disabled
      tprobe1 = 0;
    }
  }

void MANAGEMENT_tempoff(void)
{
  // temp probe stop
  if (mySetupData->get_temperatureprobestate() == 1)              // if probe enabled
  {
    DebugPrintln("temp off");
    // there is no destructor call
    mySetupData->set_temperatureprobestate(0);                    // disable probe
    myTempProbe->stop_temp_probe();                               // stop probe
    tprobe1 = 0;                                                  // indicate no probe found
  }
  mserver.send(NORMALWEBPAGE, PLAINTEXTPAGETYPE, "Temperature probe Off");
}

void MANAGEMENT_tempon(void)
{
  // temp probe start
  if ( mySetupData->get_temperatureprobestate() == 0)               // if probe is disabled
  {
    mySetupData->set_temperatureprobestate(1);                      // enable it
    if ( tprobe1 == 0 )                                             // if there was no probe found
    {
      Serial.println("Create new tempprobe");               
      myTempProbe = new TempProbe;                                  // create new instance and look for probe
    }
    else
    {
      Serial.println("myTempProbe already created");
    }
  }
  mserver.send(NORMALWEBPAGE, PLAINTEXTPAGETYPE, "Temperature probe On");
}

// ----------------------------------------------------------------------------------------------
myFP2ESP.ino
279
int   tprobe1;                               // true if a temperature probe was detected
float lasttemp;                             // last valid temp reading

1037
  tprobe1 = 0;
  lasttemp = 20.0;
  if ( mySetupData->get_temperatureprobestate() == 1)   // if temperature probe enabled then try to start new probe
  {
    myTempProbe = new TempProbe;                        // create temp probe - should set tprobe1=true if probe found
  }
  else
  {
    tprobe1 = 0;
  }

1276
  if ( mySetupData->get_temperatureprobestate() == 1)     // if temp probe "enabled" state
  {
    if ( tprobe1 != 0 )                                   // if a probe was found
    {
      DebugPrintln("tprobe1 != 0. read_temp");
      myTempProbe->read_temp(1);                          // read the temperature
    }
    else
    {
      DebugPrintln("tprobe1 is 1");
    }
  }

1508
        if ( mySetupData->get_temperatureprobestate() == 1)           // if probe is enabled
        {
          if( tprobe1 != 0 )                                          // if probe was found
          {
            DebugPrintln("loop: update_temp()");
            myTempProbe->update_temp();
          }
          else
          {
            DebugPrintln("loop: tprobe1 = 0");
          }
        }

temp.h
// ----------------------------------------------------------------------------------------------
18
remove extern byte tprobe1;

comms.h
// ----------------------------------------------------------------------------------------------
27
extern int   tprobe1;
extern float lasttemp;

155
    case 6: // get temperature
      SendPaket('Z', lasttemp, 3);

223
    case 20: // set the temperature resolution setting for the DS18B20 temperature probe
      WorkString = receiveString.substring(3, receiveString.length() - 1);
      paramval = WorkString.toInt();
      mySetupData->set_tempprecision((byte) paramval);
      if( mySetupData->get_temperatureprobestate() == 1 )     // if temp probe is enabled
      {
        if( tprobe1 != 0 )                                 // if probe was found
        {
          myTempProbe->temp_setresolution((byte) paramval);   // set probe resolution
          mySetupData->set_tempprecision((byte) paramval);    // and save for future use      
        }
      }
      break;

530
    case 83: // get if there is a temperature probe
      SendPaket('c', tprobe1);
      break;

621
case 96:
              // temp probe start
              if (mySetupData->get_temperatureprobestate() == 0)          // if temp probe disabled
              {
                mySetupData->set_temperatureprobestate(1);                // then enable probe
                if ( tprobe1 == 0 )                                       // if probe not started
                {
                  myTempProbe = new TempProbe();                          // start a new probe
                }
                else
                {
                  DebugPrintln("Probe already statrted");
                }
              }
            }
            else
            {
              // temp probe stop
              if (mySetupData->get_temperatureprobestate() == 1)          // if probe currently enabled
              {
                mySetupData->set_temperatureprobestate(0);                // then disable it
                if ( tprobe1 != 0 )                                       // only call this if a probe was found
                {
                  myTempProbe->stop_temp_probe();                          // else an exception will occur
                }
              }
            }

display.cpp
// ----------------------------------------------------------------------------------------------
36
extern float lasttemp;
197
  snprintf(buffer, sizeof(buffer), "TEMP: %.2f C", lasttemp);
  drawString(54, 54, buffer);
272
  //Temperature
  print(TEMPSTR);
  print(String(lasttemp, 2));
  println(" c");
490
  //Temperature
  print(TEMPSTR);
  print(String(lasttemp, 2));
  print(" c");
  clearToEOL();
  println();

webserver.cpp
// ----------------------------------------------------------------------------------------------
37
extern int   tprobe1;
extern float lasttemp;

778
    WSpg.replace("%MOV%", String(isMoving));

    if ( mySetupData->get_tempmode() == 1)
    {
      String tpstr = String(lasttemp, 2);
      WSpg.replace("%TEM%", tpstr);
      WSpg.replace("%TUN%", " c");
    }
    else
    {
      float ft = lasttemp;
      ft = (ft * 1.8) + 32;
      String tpstr = String(ft, 2);
      WSpg.replace("%TEM%", tpstr);
      WSpg.replace("%TUN%", " f");
    }

1085
  if ( tres_str != "" )
  {
    int temp = 0;
    DebugPrint("root() -temperature resolution:");
    DebugPrintln(tres_str);
    temp = tres_str.toInt();
    if ( temp < 9 )
    {
      // error, do not change
      temp = 9;
    }
    if ( temp > 12 )
    {
      temp = 12;
    }
    mySetupData->set_tempprecision(temp);
    if( mySetupData->get_temperatureprobestate() == 1 )       // if probe enabled
    {
      if( tprobe1 != 0 )                                      // if there was a probe found
      {
        myTempProbe->temp_setresolution((byte)temp);          // set resolution
      }
    }
  }

temp.h
// ----------------------------------------------------------------------------------------------
class TempProbe : public DallasTemperature
{
  public:

    void  start_temp_probe(void);
    void  stop_temp_probe(void);
and remove Private data

temperature.cpp
// ----------------------------------------------------------------------------------------------
// ----------------------------------------------------------------------------------------------
// temp.cpp : myFP2ESP temperature probe
// ----------------------------------------------------------------------------------------------

// ----------------------------------------------------------------------------------------------
// COPYRIGHT
// ----------------------------------------------------------------------------------------------
// (c) Copyright Robert Brown 2014-2021. All Rights Reserved.
// (c) Copyright Holger Manz, 2020-2021. All Rights Reserved.
// ----------------------------------------------------------------------------------------------

#include <Arduino.h>
#include "FocuserSetupData.h"
#include "generalDefinitions.h"
#include "myBoards.h"
#include <OneWire.h>                          // https://github.com/PaulStoffregen/OneWire
//#include <myDallasTemperature.h>
#include "temp.h"

// ----------------------------------------------------------------------------------------------
// EXTERNALS
// ----------------------------------------------------------------------------------------------
extern int   tprobe1;
extern float lasttemp;

extern SetupData *mySetupData;
extern bool TimeCheck(unsigned long, unsigned long);
extern unsigned long ftargetPosition;         // target position

// ----------------------------------------------------------------------------------------------
// DATA
// ----------------------------------------------------------------------------------------------
OneWire oneWirech1(TEMPPIN);                  // setup temperature probe
DallasTemperature sensor1(&oneWirech1);
DeviceAddress tpAddress;                      // holds address of the temperature probe

// ----------------------------------------------------------------------------------------------
// CLASS
// ----------------------------------------------------------------------------------------------
TempProbe::TempProbe()  :  DallasTemperature (&oneWirech1)
{
  start_temp_probe();
}

void TempProbe::start_temp_probe()
{
  Serial.println("start_temp_probe()");
  tprobe1 = false;
  pinMode(TEMPPIN, INPUT);                      // Configure GPIO pin for temperature probe
  DebugPrintln(CHECKFORTPROBESTR);
  Serial.println("start_temp_probe(): begin");
  begin();
  DebugPrintln(GETTEMPPROBESSTR);
  tprobe1 = getDeviceCount();                   // should return 1 if probe connected
  DebugPrint(TPROBESTR);
  DebugPrintln(tprobe1);
  if ( tprobe1 != 0 )
  {
    if (getAddress(tpAddress, 0) == true)       // get the address so we can set the probe resolution
    {
      tprobe1 = 1;                              // address was found so there was a probe
      setResolution(tpAddress, mySetupData->get_tempprecision());    // set probe resolution
      DebugPrint(SETTPROBERESSTR);
      switch (mySetupData->get_tempprecision())
      {
        case 9: DebugPrintln(F("0.5"));
          break;
        case 10: DebugPrint(F("0.25"));
          break;
        case 11: DebugPrintln(F("0.125"));
          break;
        case 12: DebugPrintln(F("0.0625"));
          break;
        default:
          DebugPrintln(F("Unknown"));
          break;
      }
      requestTemperatures();                    // request the sensor to begin a temperature reading
    }
  }
  else
  {
    DebugPrintln(TPROBENOTFOUNDSTR);
  }
}

void TempProbe::stop_temp_probe()
{
  tprobe1 = 0;
}

void TempProbe::temp_setresolution(byte rval)
{
  if ( tprobe1 != 0 )
  {
    setResolution(tpAddress, rval);             // set the probe resolution (9=0.25, 12=0.00125)
  }
  else
  {
    DebugPrintln("Cannot set resolution. No probe found.");
  }
}

float TempProbe::read_temp(byte new_measurement)
{
  static float lasttemp = 20.0;               // keep track of previous temperature value
  if (!new_measurement || ( tprobe1 == 0 ))
  {
    return lasttemp;                          // return previous measurement
  }

  float result = getTempCByIndex(0);          // get temperature, always in celsius
  DebugPrint(TEMPSTR);
  DebugPrintln(result);
  if (result > -40.0 && result < 80.0)        // avoid erronous readings
  {
    lasttemp = result;
  }
  else
  {
    result = lasttemp;
  }
  return result;
}

void TempProbe::update_temp(void)
{
  static byte tcchanged = mySetupData->get_tempcompenabled();  // keeps track if tempcompenabled changes

  if ( mySetupData->get_temperatureprobestate() == 1)
  {
    if (tprobe1 == 1)
    {
      static unsigned long lasttempconversion = 0;
      static byte requesttempflag = 0;                  // start with request
      unsigned long tempnow = millis();

      // see if the temperature needs updating - done automatically every 1.5s
      if (TimeCheck(lasttempconversion, TEMPREFRESHRATE))   // see if the temperature needs updating
      {
        static float tempval;
        static float starttemp;                         // start temperature to use when temperature compensation is enabled

        if ( tcchanged != mySetupData->get_tempcompenabled() )
        {
          tcchanged = mySetupData->get_tempcompenabled();
          if ( tcchanged == 1 )
          {
            starttemp = read_temp(1);
          }
        }

        lasttempconversion = tempnow;                   // update time stamp

        if (requesttempflag)
        {
          tempval = read_temp(1);
        }
        else
        {
          requestTemperatures();
        }

        requesttempflag ^= 1; // toggle flag

        if (mySetupData->get_tempcompenabled() == 1)    // check for temperature compensation
        {
          if ((abs)(starttemp - tempval) >= 1)          // calculate if temp has moved by more than 1 degree
          {
            unsigned long newPos;
            byte temperaturedirection;                  // did temperature fall (1) or rise (0)?
            temperaturedirection = (tempval < starttemp) ? 1 : 0;
            if (mySetupData->get_tcdirection() == 0)    // check if tc direction for compensation is inwards
            {
              // temperature compensation direction is in, if a fall then move in else move out
              if ( temperaturedirection == 1 )          // check if temperature is falling
              {
                newPos = ftargetPosition - mySetupData->get_tempcoefficient();    // then move inwards
              }
              else
              {
                newPos = ftargetPosition + mySetupData->get_tempcoefficient();    // else move outwards
              }
            }
            else
            {
              // temperature compensation direction is out, if a fall then move out else move in
              if ( temperaturedirection == 1 )
              {
                newPos = ftargetPosition + mySetupData->get_tempcoefficient();
              }
              else
              {
                newPos = ftargetPosition - mySetupData->get_tempcoefficient();
              }
            }
            newPos = (newPos > mySetupData->get_maxstep()) ? mySetupData->get_maxstep() : newPos;
            // newPos should be checked for < 0 but cannot due to unsigned
            // newPos = (newPos < 0 ) ? 0 : newPos;
            ftargetPosition = newPos;
            starttemp = tempval;                        // save this current temp point for future reference
          } // end of check for tempchange >=1
        } // end of check for tempcomp enabled
      } // end of check for temperature needs updating
    } // end of if tprobe
    else
    {
      DebugPrintln("Cannot update_temp. No probe found.");
    }
  }
  else
  {
    DebugPrintln("Cannot update_temp. Probe not enabled.");
  }
}

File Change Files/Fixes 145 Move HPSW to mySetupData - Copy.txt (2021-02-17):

Move HPSW to mySetupData

changes to msindex2.html
<h3 style="color: #%HEC%">HOME POSITION SWITCH</h3><p>%HPO%</p>

generalDefinitions.h
#define ENABLEHPSWSTR             "<form action=\"/msindex2\" method=\"post\"><b>State</b> [%HPL%]: <input type=\"hidden\" name=\"hpswon\" value=\"true\"><input type=\"submit\" value=\"ENABLE\"></form>"
#define DISABLEHPSWSTR            "<form action=\"/msindex2\" method=\"post\"><b>State</b> [%HPL%]: <input type=\"hidden\" name=\"hpswoff\" value=\"true\"><input type=\"submit\" value=\"DISABLE\"></form>"

myFP2ESP.ino
323
bool HPS_alert()
{
  if ( mySetupData->get_homepositionswitch() == 1)
  {
    return !((bool)digitalRead(HPSWPIN));
  }
  else
  {
    return false;
  }
}

806
void init_homepositionswitch()
{
  if ( mySetupData->get_homepositionswitch() == 1)
  {
    pinMode(HPSWPIN, INPUT_PULLUP);
  }
}

1276
  // setup home position switch input pin
  init_homepositionswitch();

1385 remove #ifdef
  int stepstaken = 0;
  bool hpswstate = false;

1698
    case State_SetHomePosition:                         // move out till home position switch opens
      DebugPrintln("State_SetHomePosition");
      if( mySetupData->get_homepositionswitch() == 1)
      {

      }
      MainStateMachine = State_DelayAfterMove;
      TimeStampDelayAfterMove = millis();
      DebugPrintln(STATEDELAYAFTERMOVE);
      break;

comms.h
38
extern void init_homepositionswitch(void);

411
    case 50: // Get if Home Position Switch enabled, 0 = no, 1 = yes
      if ( mySetupData->get_homepositionswitch() == 1)
      {
        SendPaket('l', 1);
      }
      else
      {
        SendPaket('l', 0);
      }
      break;

472
    case 63: // get status of home position switch (0=off, 1=closed, position 0)
      if ( mySetupData->get_homepositionswitch() == 1)
      {
        SendPaket('H', digitalRead(HPSWPIN));
      }
      else
      {
        SendPaket('H', "0");
      }
      break;

712
    case 99:  // set homepositonswitch state, 0 or 1
      {
        int enablestate = 0;
        WorkString = receiveString.substring(3, receiveString.length() - 1);
        enablestate = WorkString.toInt();
        mySetupData->set_homepositionswitch(enablestate);
        if( enablestate == 1 )
        {
          init_homepositionswitch();
        }
      }
      break;

FocuserSetupData.h
class SetupData
{
  public:

    int get_homepositionswitch();
    void set_homepositionswitch(int);

    int homepositionswitch;

FocuserSetupData.cpp
124
      this->homepositionswitch    = doc_per["hpsw"];
228
  this->homepositionswitch    = 0;
359
  doc["hpsw"]               = this->homepositionswitch;
631
int SetupData::get_homepositionswitch()
{
  return this->homepositionswitch;
}
843
void SetupData::set_homepositionswitch(int newval)
{
  this->StartDelayedUpdate(this->homepositionswitch, newval);
}

managementserver.cpp
66
extern void init_homepositionswitch(void);
981
    if ( mySetupData->get_homepositionswitch() == 1)
    {
      MSpg.replace("%HPO%", String(DISABLEHPSWSTR));   // button
      MSpg.replace("%HPL%", String(ENABLEDSTR));       // state
    }
    else
    {
      MSpg.replace("%HPO%", String(ENABLEHPSWSTR));
      MSpg.replace("%HPL%", String(NOTENABLEDSTR));
    }
1354
  // HOME POSITION SWITCH, enable, disable
  msg = mserver.arg("hpswon");
  if ( msg != "" )
  {
    // if current state is disabled then enable
    if ( mySetupData->get_homepositionswitch() == 0)
    {
      mySetupData->set_homepositionswitch(1);
      init_homepositionswitch();
    }
  }
  msg = mserver.arg("hpswoff");
  if ( msg != "" )
  {
      mySetupData->set_homepositionswitch(0);
  }
1941
  else if ( mserver.argName(0) == "hpsw" )
  {
    jsonstr = "{ \"hpsw\":" + String(mySetupData->get_homepositionswitch()) + " }";
    MANAGEMENT_sendjson(jsonstr);
  }
2172
  value = mserver.arg("hpsw");
  if ( value != "" )
  {
    DebugPrint("hpsw:");
    DebugPrintln(value);
    if ( value == "on" )
    {
      mySetupData->set_homepositionswitch(1);
      init_homepositionswitch();
      rflag = true;
    }
    else if ( value == "off" )
    {
      mySetupData->set_homepositionswitch(0);
      rflag = true;
    }
  }

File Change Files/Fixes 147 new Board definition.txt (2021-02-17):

GeneralDefinitions.cpp
99
const char* HPMOVEOUTSTEPSSTR     = "HP Sw, Mov out steps:";

myBoardTypes.h
65
#ifndef WEMOSDRV8825H
#define WEMOSDRV8825H         50         // this is for Holger
#endif

myBoards.h
??
//#define DRVBOARD WEMOSDRV8825H

75?
#if (DRVBRD == WEMOSDRV8825H )          // Holger's WEMOS, special settings
#define TEMPPIN       4
#define I2CDATAPIN    4
#define I2CCLKPIN     5
#define DIRPIN        13                // D7 GPIOP13
#define STEPPIN       12                // D6 GPIO12
#define ENABLEPIN     14                // D5 GPIO14
#define MSPEED        2000
#endif

myBoards.cpp
17
#if DRVBRD == WEMOSDRV8825H
const char* DRVBRD_ID = "WEMOSDRV8825H";
#elif DRVBRD == WEMOSDRV8825

193
#if (DRVBRD == WEMOSDRV8825 || DRVBRD == PRO2EDRV8825 || DRVBRD == PRO2ESP32R3WEMOS || DRVBRD == WEMOSDRV8825H )

309
#if (DRVBRD == WEMOSDRV8825 || DRVBRD == PRO2EDRV8825 || DRVBRD == PRO2ESP32R3WEMOS || DRVBRD == WEMOSDRV8825H)

385
#if (DRVBRD == WEMOSDRV8825 || DRVBRD == PRO2EDRV8825 || DRVBRD == PRO2ESP32DRV8825 || DRVBRD == PRO2ESP32R3WEMOS || DRVBRD == WEMOSDRV8825H)

393
#if (DRVBRD == WEMOSDRV8825 || DRVBRD == PRO2EDRV8825 || DRVBRD == PRO2ESP32DRV8825 || DRVBRD == PRO2ESP32R3WEMOS || DRVBRD == WEMOSDRV8825H)

420
#if (DRVBRD == WEMOSDRV8825 || DRVBRD == PRO2EDRV8825 || DRVBRD == PRO2ESP32DRV8825 || DRVBRD == PRO2ESP32R3WEMOS || DRVBRD == WEMOSDRV8825H)

456
#endif // #if (DRVBRD == WEMOSDRV8825 || DRVBRD == PRO2EDRV8825 || DRVBRD == PRO2ESP32DRV8825 || DRVBRD == PRO2ESP32R3WEMOS || DRVBRD == WEMOSDRV8825H)

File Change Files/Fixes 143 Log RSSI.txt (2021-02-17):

myFP2ESP.ino
266
long  rssi;                                  // network signal strength

799 insert code
long getrssi()
{
  long strength = WiFi.RSSI();
  return strength;
}

1185
#if defined(ACCESSPOINT) || defined(STATIONMODE)
  rssi = getrssi();                          // get network strength
  // Starting TCP Server

comms.h
29
extern long rssi;
36
extern long getrssi(void);
698
    case 98:
      {
        long rssi = getrssi();
        SendPaket('s', rssi);
      }
      break;

ManagementServer.cpp
53 delete
extern long rssi;
65
extern long getrssi(void);

2260
void MANAGEMENT_rssi(void)
{
  long rssi = getrssi();
  mserver.send(NORMALWEBPAGE, PLAINTEXTPAGETYPE, String(rssi) );
}

1905
  else if ( mserver.argName(0) == "rssi" )
  {
    long rssi = getrssi();
    jsonstr = "{ \"rssi\":" + String(rssi) + " }";
    MANAGEMENT_sendjson(jsonstr);
  }

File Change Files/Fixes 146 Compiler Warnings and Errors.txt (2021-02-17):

compiler warnings
managementserver.cpp
1678
    for ( unsigned int i = 0; i < tp.length(); i++)     // check for 0 or 1
2070
    ftargetPosition = ( temp > mySetupData->get_maxstep()) ? mySetupData->get_maxstep() : temp;
2083
    ftargetPosition = ( temp > mySetupData->get_maxstep()) ? mySetupData->get_maxstep() : temp;

myFP2ESP.ino
1105
  WiFi.begin(mySSID, myPASSWORD); // attempt to start the WiFi
1141
    memcpy( myPASSWORD, myPASSWORD_1, (sizeof(myPASSWORD_1) / sizeof(myPASSWORD_1[0])) );
1143
    WiFi.begin(mySSID, myPASSWORD);  // attempt to start the WiFi

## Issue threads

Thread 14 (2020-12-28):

Some text on tablet or phone too small to read

brownrb, 2020-12-28:
When using a tablet or phone, some text is too small to read.

brownrb, 2020-12-28:
I know what it is and will update the html files shortly. I will create a new branch to handle this.

brownrb, 2020-12-28:
Fix done and merged back to master
Required
<meta name="viewport" content="width=device-width, initial-scale=1">
to be pasted in html files within <head>  </head>

Closed 2020-12-28.

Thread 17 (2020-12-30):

Home Position Switch not working

hcomet, 2020-12-30:
The home position switch code looks to have been rewritten since release 122. The new code relies on HPS_alert which is defined in generalDefinitions.h using:

#ifdef HOMEPOSITIONSWITCH
#define HPS_alert             !((bool)digitalRead(HPSWPIN))
#else
#define HPS_alert             false
#endif

Unfortunately HOMEPOSITIONSWITCH is defined in focuserconfig.h which is included in myFP2ESP.ino after the include for generalDefinitions.h. This results in HOMEPOSITIONSWITCH never being defined when checked by the ifdef in generalDefinitions.h so the value of HPS_alert is always false disabling the homing switch.

I also tried the new homing switch test: HOMEPOSITIONSWITCH2 but it suffers from the same issue, HOMEPOSITIONSWITCH is never defined so HPS_alert is never properly defined in generalDefinitions.h.

hcomet, 2020-12-30:
I should have mentioned that I found this issue with the release 135 that was on sourceforge but it looks like the latest master on github has the same code structure and issue, Couldn't confirm because I can't compile (see other issue).

BTW: since the Windows app has a check homing switch state function I was surprised that it does work.  Looks life the response to that query skips the use of HPS_alert and returns the actual pin state.

brownrb, 2021-01-02:
I see and understand the problem
The code in generalDefinitions.h
#ifdef HOMEPOSITIONSWITCH
#define HPS_alert             !((bool)digitalRead(HPSWPIN))
#else
#define HPS_alert             false
#endif
cannot possibly work because HOMEPOSITION has not been defined. HOMEPOSITION is only defined in focuserconfig.h which is not referenced by generalDefinitions.h and focuserconfig.h is only included later on in the compile stage.

HPS_alert is a macro and thus not easily changed. HPS_alert is used in myBoards.cpp and the main ino file.
It is difficult to place this into myBoards.h because that is not exposed to focuserconfig.h either.

it cannot be placed into focuserconfig.h because generalDefinitions.h/.cpp and myboards.h/.cpp do not reference focuserconfig.h either

I am working on it

brownrb, 2021-01-03:
I have applied the fix directly into master branch. HPSW should now work.
Version number 135

Closed 2021-01-03.

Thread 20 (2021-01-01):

Reverse motor direction not working

alros100, 2021-01-01:
ESP8266
135 version firmware (last one prior to move to github)
myespfp2esp version 2.0.3.25
also ascom driver

motor reverse direction checkbox does not appear to function.

same rig works with arduino nano

thanks
Al

brownrb, 2021-01-02:
The Windows app myFP2ESP definately seems to be sending the correct commands to reverse the motor direction.

It looks like it is a firmware issue. I confirtm reverse direction does not work:
data_per.jsn is clearly being updated with new reverse direction state:
Web server is clearly reporting new reverse direction state:
Motor keeps rotating in same direction as before the change.
Tested and confirmed not working with v129 and latest version Jan 01-2021

brownrb, 2021-01-02:
Am working on fix and other updates

brownrb, 2021-01-02:
Resolved in branch 134 update - now merged into Master

Closed 2021-01-02.

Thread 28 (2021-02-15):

Using the Management Server to enable the temperature probe causes a reboot

brownrb, 2021-02-15:
Using the Management Server to enable the temperature probe causes a reboot.

I manually set "tprobe" to 1 in the data_per.jsn and upload it, power cycle and then the temperature probe works fine.

I can then disable through the Management Server but if I try Enable again then it reboots the focuser.

brownrb, 2021-02-15:
I have tracked this down and know the cause.

Fixing it is a bit more involved.

I should have a solution very soon.

brownrb, 2021-02-16:
Fixed in branch 142
https://github.com/brownrb/myFP2EFirmware/releases
applied to Master

Closed 2021-02-16.

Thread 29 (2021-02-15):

Homeswitch works but it takes a few tries to back away from it

brownrb, 2021-02-15:
Homeswitch works but it takes a few tries to back away from it.

Usually have to +10 two or three times before it disengages the homeswitch.

Maybe this is a backlash setting issue on my side but it seemed to work fine in the previous release

brownrb, 2021-02-15:
I have created a new branch 141.
I think I may have a quick fix for this, so I will code it into branch 141
When it is ready for testing, I will let you know,

regards
R

brownrb, 2021-02-15:
I have the code for handling HPSW when backlash is enabled - uploaded to Branch 141
Can you please download branch 141 to test it please.

At the same time I fixed a couple of other things that were an issue
141
Change driverboard->halt() - no need to return stepcount
Fix for using Serial.print commands in MachineStateBacklash - changed to DebugPrint
Fix for 2nd network credential not being updated [readwificonifg() ]
Fix for Home Position Switch not working in Backlash
Fix for compilation warning message about driverboard->halt() - I have changed this to type void as there is no need for the function to return a value.

hcomet, 2021-02-15:
I tried 141. Still have the same issue. Seems like the backing away from the switch after contact doesn't happen. I tried it with and without backlash enabled and has the same result for both.

I have a rack and pinion focuser with the Nema 14 - PG27 focuser. My backlash is set to 60 steps in both directions.

hcomet, 2021-02-15:
Okay, I think I found the issue. I added a call to delayMicroseconds inside the loop that backs the focuser away from the homeswitch. I saw this was done in the backlash code. This seemed to fix things and the back away works and I'm no longer stuck on the homeswitch.

I also noticed that the first move after the homeswitch back off also causes a backlash compensation which it shouldn't. So I also reset the direction to align with the switch backoff with set_focuserdirection.

Here's the State_SetHomePosition case with the two addtional lines:

```
    case State_SetHomePosition:                         // move out till home position switch opens
      DebugPrintln("State_SetHomePosition");
#ifdef HOMEPOSITIONSWITCH
      // check if display home position switch messages is enabled
      if ( mySetupData->get_showhpswmsg() == 1)
      {
        if (mySetupData->get_displayenabled() == 1)
        {
          myoled->oledtextmsg(HPMOVETILLOPENSTR, -1, false, true);
        }
      }
      // HOME POSITION SWITCH IS CLOSED - Step out till switch opens then set position = 0
      stepstaken = 0;                                   // Count number of steps to prevent going too far
      DebugPrintln(HPMOVETILLOPENSTR);
      DirOfTravel = !DirOfTravel;                       // We were going in, now we need to reverse and go out
      hpswstate = HPSWCLOSED;                           // We know we got here because switch was closed
      while ( hpswstate == HPSWCLOSED )
      {
        if ( mySetupData->get_reversedirection() == 0 )
        {
          steppermotormove(DirOfTravel);                // take 1 step
        }
        else
        {
          steppermotormove(!DirOfTravel);
        }

        delayMicroseconds(driverboard->getstepdelay()); // Ensure delay between steps

        stepstaken++;                                   // increment steps taken
        if ( stepstaken > HOMESTEPS )                   // this prevents the endless loop if the hpsw is not connected or is faulty
        {
          DebugPrintln(HPMOVEOUTERRORSTR);
          hpswstate = HPSWOPEN;
        }
        else
        {
          hpswstate = !(digitalRead(HPSWPIN));          // read state of HPSW
        }
      }
      DebugPrint(F(HPMOVEOUTSTEPSSTR));
      DebugPrintln(stepstaken);
      DebugPrintln(F(HPMOVEOUTFINISHEDSTR));
      ftargetPosition = 0;
      driverboard->setposition(0);
      mySetupData->set_fposition(0);

      mySetupData->set_focuserdirection(DirOfTravel);

      if ( mySetupData->get_showhpswmsg() == 1)         // check if display home position switch messages is enabled
      {
        if (mySetupData->get_displayenabled() == 1)
        {
          myoled->oledtextmsg(HPMOVEOUTFINISHEDSTR, -1, true, true);
        }
      }
#endif // #ifdef HOMEPOSITIONSWITCH
      MainStateMachine = State_DelayAfterMove;
      TimeStampDelayAfterMove = millis();
      DebugPrintln(STATEDELAYAFTERMOVE);
      break;
```

brownrb, 2021-02-16:
Fixed in Master

Closed 2021-02-16.

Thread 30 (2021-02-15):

Please move #HOMEPOSITIONSWITCH to mySetupData

brownrb, 2021-02-15:
This will remove #define HOMEPOSITIONSWITCH out of focuserconfig.h file and means a user can simply enable/disable it via webserver page if needed -

There is a requirement to reboot the controller once the HPSW is enabled though?
may need to init the pin as input as part of the enable code.

brownrb, 2021-02-16:
Slated for 144 release

brownrb, 2021-02-16:
Done, Branch 145, merged with Master

Closed 2021-02-16.

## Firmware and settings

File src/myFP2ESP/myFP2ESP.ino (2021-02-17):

// ----------------------------------------------------------------------------------------------
// TITLE: myFP2ESP FIRMWARE OFFICIAL RELEASE 147
// ----------------------------------------------------------------------------------------------
// myFP2ESP - Firmware for ESP8266 and ESP32 myFocuserPro2 WiFi Controllers
// Supports Driver boards DRV8825, ULN2003, L298N, L9110S, L293DMINI, L293D
// ESP8266  OLED display, Temperature Probe
// ESP32    OLED display, Temperature Probe, Push Buttons, In/Out LED's,
//          Infrared Remote, Bluetooth
// Supports modes, ACCESSPOINT, STATIONMODE, BLUETOOTH, LOCALSERIAL, WEBSERVER,
//          ASCOMREMOTE
// Remember to change your target CPU depending on board selection

// ----------------------------------------------------------------------------------------------
// COPYRIGHT
// ----------------------------------------------------------------------------------------------
// (c) Copyright Robert Brown 2014-2021. All Rights Reserved.
// (c) Copyright Holger M, 2019-2021. All Rights Reserved.
// (c) Copyright Pieter P - OTA code and SPIFFs file handling/upload based on examples

// ----------------------------------------------------------------------------------------------
// SPECIAL LICENSE
// ----------------------------------------------------------------------------------------------
// This code is released under license. If you copy or write new code based on
// the code in these files. you MUST include to link to these files AND you MUST
// include references to the authors of this code.

// ----------------------------------------------------------------------------------------------
// CONTRIBUTIONS
// ----------------------------------------------------------------------------------------------
// It is costly to continue development and purchase boards and components.
// Your support is needed to continue development of this project. Please
// contribute to this project, and use PayPal to send your donation to user
// rbb1brown@gmail.com (Robert Brown). All contributions are gratefully accepted.

// ----------------------------------------------------------------------------------------------
// TO PROGRAM THE FIRMWARE
// ----------------------------------------------------------------------------------------------
// 1. Set your DRVBRD in myBoards.h so the correct driver board is used
// 2. Set the correct hardware options/controller modes in focuserconfig.h
//    to match your hardware
// 3. Set your target CPU to match the correct CPU for your board
// 4. Compile and upload to your controller

// ----------------------------------------------------------------------------------------------
// PCB BOARDS
// ----------------------------------------------------------------------------------------------
// The PCB's are available as GERBER files.
// https://sourceforge.net/projects/myfocuserpro2-esp32/files/PCB%20Gerber%20Files/
//
// L293D Shield  https://www.ebay.com/itm/L293D-Motor-Drive-Shield-Wifi-Module-For-Arduino-NodeMcu-Lua-ESP8266-ESP-12E/292619874436
// ESP32 R3WEMOS https://www.ebay.com/itm/R3-Wemos-UNO-D1-R32-ESP32-WIFI-Bluetooth-CH340-Devolopment-Board-For-Arduino/264166013552
// ----------------------------------------------------------------------------------------------
// COMPILE ENVIRONMENT : Tested with
// Arduino IDE 1.8.13
// ESP8266 Core 2.7.4
// ESP32 Core 1.0.4
// Libraries
// Arduino JSON 6.15.2
// myOLED as in myFP2ELibs
// IRRemoteESP32 as in myFP2ELibs
// HalfStepperESP32 as in myFP2ELibs
// myDallas Temperature 3.7.3A as in myFP2ELibs
// Wire [as installed with Arduino 1.8.13
// OneWire 2.3.5
// EasyDDNS 1.5.9
// Notes:
// You may need to turn 12V off to reprogram chip. Speed is 115200. Sometimes
// you might need to remove the chip from PCB before re-programming new firmware.
// Remember to remove WIFI library as instructed in PDF when programming ESP32
// or ESP8266.

// ----------------------------------------------------------------------------------------------
// 1: SPECIFY DRIVER BOARD in myBoards.h
// ----------------------------------------------------------------------------------------------
// Please specify your driver board in myBoards.h, only 1 can be defined, see DRVBRD line

#include "generalDefinitions.h"
#include "myBoards.h"

// ----------------------------------------------------------------------------------------------
// 2: FOR ALL ESP8266 BOARDS AND R3-WEMOS-ESP32 USING DRV8825 SET DRV8825STEPMODE in myBoards.h
// ----------------------------------------------------------------------------------------------
// SET DRV8825STEPMODE in myBoards.h to the correct value

// ----------------------------------------------------------------------------------------------
// 3: FOR ULN2003, L293D, L293DMINI, L298N, L9110S specify STEPSPERREVOLUTION in myBoards.h
// ----------------------------------------------------------------------------------------------
// You MUST set STEPSPERREVOLUTION to the correct value in myBoards.h

// ----------------------------------------------------------------------------------------------
// 4: SPECIFY HARDWARE OPTIONS IN focuserconfig.h
// ----------------------------------------------------------------------------------------------
// Specify your controller options in focuserconfig.h, such as OLEDTEXT

// ----------------------------------------------------------------------------------------------
// 5: SPECIFY THE CONTROLLER MODE IN focuserconfig.h
// ----------------------------------------------------------------------------------------------
// Please specify your controller mode in focuserconfig.h, such as ACCESSPOINT
// and MANAGEMENT

// ----------------------------------------------------------------------------------------------
// 6: INCLUDES
// ----------------------------------------------------------------------------------------------
#include "focuserconfig.h"

#undef DEBUG_ESP_HTTP_SERVER                // needed sometimes to prevent serial output from WiFiServerlibrary

#include <WiFiServer.h>
#include <WiFiClient.h>
#include <ArduinoJson.h>

#if defined(ESP8266)                        // this "define(ESP8266)" comes from Arduino IDE
#undef DEBUG_ESP_HTTP_SERVER                // prevent messages from WiFiServer 
#include <ESP8266WiFi.h>
#include <FS.h>                             // include the SPIFFS library  
#else                                       // otherwise assume ESP32
#include <WiFi.h>
#include "SPIFFS.h"
#endif
#include <SPI.h>
#include "FocuserSetupData.h"

// --------------------------------------------------------------------------
// 7: WIFI NETWORK SSID AND PASSWORD CONFIGURATION
// --------------------------------------------------------------------------
// 1. For access point mode this is the network you connect to
// 2. For station mode, change mySSID and myPASSWORD to match your network details

char mySSID[64]     = "myfp2eap";
char myPASSWORD[64] = "myfp2eap";

// Alternative network credentials if initial details above did not work
char mySSID_1[64]     = "FireFox";            // alternate network id
char myPASSWORD_1[64] = "AllYeWhoEnter";      // alternate network id

// ----------------------------------------------------------------------------------------------
// 8: OTAUPDATES (OVER THE AIR UPDATE) SSID AND PASSWORD CONFIGURATION
// ----------------------------------------------------------------------------------------------
// You can change the values for OTANAME and OTAPassword if required
#ifdef OTAUPDATES
#include <ArduinoOTA.h>

const char *OTAName = "ESP8266";            // the username and password for the OTA service
const char *OTAPassword = "esp8266";
#endif // #ifdef OTAUPDATES

// ----------------------------------------------------------------------------------------------
// 9: BLUETOOTH MODE NAME:
// ----------------------------------------------------------------------------------------------
#ifdef BLUETOOTHMODE
String BLUETOOTHNAME = "MYFP3ESP32BT";      // default name for Bluetooth controller, this name you can change
#endif // #ifdef BLUETOOTHMODE

// ----------------------------------------------------------------------------------------------
// 10: mDNS NAME: Name must be alphabetic chars only, lowercase
// ----------------------------------------------------------------------------------------------
#ifdef MDNSSERVER
char mDNSNAME[] = "myfp2eap";               // mDNS name will be myfp2eap.local
#endif // #ifdef MDNSSERVER

// ----------------------------------------------------------------------------------------------
// 11: DUCKDNS DOMAIN AND TOKEN CONFIGURATION
// ----------------------------------------------------------------------------------------------
// if using DuckDNS you need to set these next two parameters, duckdnsdomain
// and duckdnstoken, BUT you cannot use DuckDNS with ACCESSPOINT, BLUETOOTHMODE
// or LOCALSERIAL mode
#ifdef USEDUCKDNS
const char* duckdnsdomain = "myfp2erobert.duckdns.org";
const char* duckdnstoken = "0a0379d5-3979-44ae-b1e2-6c371a4fe9bf";
#endif // #ifdef USEDUCKDNS

// ----------------------------------------------------------------------------------------------
// 12: STATIC IP ADDRESS CONFIGURATION
// ----------------------------------------------------------------------------------------------
// must use static IP if using duckdns or as an Access Point
#ifndef STATICIPON
#define STATICIPON    1
#endif
#ifndef STATICIPOFF
#define STATICIPOFF   0
#endif
//int staticip = STATICIPON;                  // IP address specified by controller - must be defined correctly
int staticip = STATICIPOFF;                   // IP address is generated by network device and is dynamic and can change

#ifdef ACCESSPOINT
// By default the Access point should be 192.168.4.1 - DO NOT CHANGE
IPAddress ip(192, 168, 4, 1);                 // AP static IP - you can change these values to change the IP
IPAddress dns(192, 168, 4, 1);                // just set it to the same IP as the gateway
IPAddress gateway(192, 168, 4, 1);
IPAddress subnet(255, 255, 255, 0);
#endif // #ifdef ACCESSPOINT

#ifdef STATIONMODE
// These need to reflect your current network settings - 192.168.x.21 - change x
// This has to be within the range for dynamic ip allocation in the router
// No effect if staticip = STATICIPOFF
IPAddress ip(192, 168, 2, 21);                // station static IP - you can change these values to change the IP
IPAddress dns(192, 168, 2, 1);                // just set it to the same IP as the gateway
IPAddress gateway(192, 168, 2, 1);
IPAddress subnet(255, 255, 255, 0);
#endif // #ifdef STATIONMODE

// ----------------------------------------------------------------------------------------------
// 13: BLUETOOTH MODE - Do not change
// ----------------------------------------------------------------------------------------------
#ifdef BLUETOOTHMODE
#include "BluetoothSerial.h"                  // needed for Bluetooth comms
#if !defined(CONFIG_BT_ENABLED) || !defined(CONFIG_BLUEDROID_ENABLED)
#error Bluetooth is not enabled! Please run `make menuconfig` to and enable it
#endif

BluetoothSerial SerialBT;                     // define BT adapter to use
#endif // BLUETOOTHMODE

// ----------------------------------------------------------------------------------------------
// 14: FIRMWARE CODE START - INCLUDES AND LIBRARIES
// ----------------------------------------------------------------------------------------------

// Project specific includes - DO NOT CHANGE
#if defined(BLUETOOTHMODE) || defined(LOCALSERIAL)
#include "ESPQueue.h"                         // by Steven de Salas
Queue queue(QUEUELENGTH);                     // receive serial queue of commands
#ifdef LOCALSERIAL
String serialline;                            // buffer for serial data
#endif
#ifdef BLUETOOTHMODE
String btline;                                // buffer for serial data
#endif
#endif // #if defined(BLUETOOTHMODE) || defined(LOCALSERIAL)

#if defined(ACCESSPOINT) || defined(STATIONMODE)
IPAddress ESP32IPAddress;
String ServerLocalIP;
WiFiServer myserver(SERVERPORT);
WiFiClient myclient;                          // only one client supported, multiple connections denied
IPAddress myIP;
#endif // #if defined(ACCESSPOINT) || defined(STATIONMODE)

#include "temp.h"
TempProbe *myTempProbe;

#include "displays.h"
OLED_NON *myoled;

// ----------------------------------------------------------------------------------------------
// 15: GLOBAL DATA -- DO NOT CHANGE
// ----------------------------------------------------------------------------------------------

//           reversedirection
//__________________________________
//               0   |   1
//__________________________________
//moving_out  1||  1   |   0
//moving_in   0||  0   |   1

DriverBoard* driverboard;

unsigned long ftargetPosition;              // target position
volatile bool halt_alert;

boolean displayfound;
byte    isMoving;                           // is the motor currently moving
char    ipStr[16];                          // shared between BT mode and other modes
const char ip_zero[] = "0.0.0.0";

long  rssi;                                 // network signal strength
int   packetsreceived;
int   packetssent;
bool  mdnsserverstate;                      // states for services, RUNNING | STOPPED
bool  webserverstate;
bool  ascomserverstate;
bool  ascomdiscoverystate;
bool  managementserverstate;
bool  tcpipserverstate;
bool  otaupdatestate;
bool  duckdnsstate;
bool  displaystate;
bool  reboot;                               // flag used to indicate a reboot has occurred
int   tprobe1;                              // true if a temperature probe was detected
float lasttemp;                             // last valid temp reading

SetupData *mySetupData;                     // focuser data

#if defined(ESP8266)
#include <ESP8266WebServer.h>
#else
#include <WebServer.h>
#endif // if defined(esp8266)

#if defined(ESP8266)
#undef DEBUG_ESP_HTTP_SERVER
extern ESP8266WebServer mserver;
#else
extern WebServer mserver;
#endif // if defined(esp8266)

extern String MSpg;
extern void start_management(void);
extern void start_ascomremoteserver(void);
extern void checkASCOMALPACADiscovery(void);

#if defined(ESP8266)
extern ESP8266WebServer *ascomserver;
#else
extern WebServer *ascomserver;
#endif // if defined(esp8266)

extern void start_webserver(void);
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
void loop()
{
  static StateMachineStates MainStateMachine = State_Idle;
  static uint32_t backlash_count = 0;
  static bool DirOfTravel = (bool) mySetupData->get_focuserdirection();
  static uint32_t TimeStampDelayAfterMove = 0;
  static uint32_t TimeStampPark = millis();
  static bool Parked = mySetupData->get_coilpower();
  static uint8_t updatecount = 0;
  static uint32_t steps = 0;

  static connection_status ConnectionStatus = disconnected;
  static oled_state oled = oled_on;

  int stepstaken = 0;
  bool hpswstate = false;

#ifdef TIMELOOP
  Serial.print("loop(): ");
  Serial.println(millis());
#endif

#if defined(ACCESSPOINT) || defined(STATIONMODE)
  if (ConnectionStatus == disconnected)
  {
    myclient = myserver.available();
    if (myclient)
    {
      DebugPrintln(TCPCLIENTCONNECTSTR);
      if (myclient.connected())
      {
        ConnectionStatus = connected;
      }
    }
  }
  else
  {
    // is data available from the client request
    if (myclient.connected())
    {
      if (myclient.available())
      {
        ESP_Communication(); // Wifi communication
      }
    }
    else
    {
      DebugPrintln(TCPCLIENTDISCONNECTSTR);
      myclient.stop();
      ConnectionStatus = disconnected;
      oled = oled_on;
    }
  }
#endif // defined(ACCESSPOINT) || defined(STATIONMODE)

#ifdef BLUETOOTHMODE
  if ( SerialBT.available() )
  {
    processbt();
  }
  // if there is a command from Bluetooth
  if ( queue.count() >= 1 )                 // check for serial command
  {
    ESP_Communication();
  }
#endif // ifdef Bluetoothmode

#ifdef LOCALSERIAL
  // if there is a command from Serial port
  if ( Serial.available() )
  {
    processserial();
  }
  if ( queue.count() >= 1 )                 // check for serial command
  {
    halt_alert = ESP_Communication();
  }
#endif // ifdef LOCALSERIAL

#ifdef OTAUPDATES
  if ( otaupdatestate == RUNNING )
  {
    ArduinoOTA.handle();                      // listen for OTA events
  }
#endif // ifdef OTAUPDATES

  if ( ascomserverstate == RUNNING)
  {
    ascomserver->handleClient();
    checkASCOMALPACADiscovery();
  }

  if ( webserverstate == RUNNING )
  {
    webserver->handleClient();
  }

#ifdef MANAGEMENT
  if ( managementserverstate == RUNNING )
  {
    mserver.handleClient();
  }
#endif

  //_____________________________MainMachine _____________________________

  switch (MainStateMachine)
  {
    case State_Idle:
      if (driverboard->getposition() != ftargetPosition)
      {
        isMoving = 1;
        driverboard->enablemotor();
        MainStateMachine = State_InitMove;
        DebugPrint(STATEINITMOVE);
        DebugPrint(CURRENTPOSSTR);
        DebugPrintln(driverboard->getposition());
        DebugPrint(TARGETPOSSTR);
        DebugPrintln(ftargetPosition);
      }
      else
      {
        // focuser stationary. isMoving is 0
        if (mySetupData->SaveConfiguration(driverboard->getposition(), DirOfTravel)) // save config if needed
        {
          oled = oled_off;
          DebugPrint(CONFIGSAVEDSTR);
        }

#ifdef PUSHBUTTONS
        update_pushbuttons();
#endif
#ifdef JOYSTICK1
        update_joystick1();
#endif
#ifdef JOYSTICK2
        update_joystick2();
#endif
#ifdef INFRAREDREMOTE
        update_irremote();
#endif
        if (mySetupData->get_displayenabled() == 1)
        {
          myoled->update_oledtextdisplay();
        }
        else
        {
          oled = oled_off;
        }
        myoled->Update_Oled(oled, ConnectionStatus);

        if ( mySetupData->get_temperatureprobestate() == 1)           // if probe is enabled
        {
          if ( tprobe1 != 0 )                                         // if probe was found
          {
            DebugPrintln("loop: update_temp()");
            myTempProbe->update_temp();
          }
          else
          {
            DebugPrintln("loop: tprobe1 = 0");
          }
        }

        if (Parked == false)
        {
          if (TimeCheck(TimeStampPark, MotorReleaseDelay))   //Power off after MotorReleaseDelay
          {
            // need to obey rule - can only release motor if coil power is disabled
            if ( mySetupData->get_coilpower() == 0 )
            {
              driverboard->releasemotor();
              DebugPrintln(RELEASEMOTORSTR);
            }
            Parked = true;
          } // if (TimeCheck(TimeStampPark, MotorReleaseDelay))
        } // if (Parked == false)
      } // if (driverboard->getposition() != ftargetPosition)
      break;

    case State_InitMove:
      isMoving = 1;
      backlash_count = 0;
      DirOfTravel = (ftargetPosition > driverboard->getposition()) ? moving_out : moving_in;
      driverboard->enablemotor();
      if (mySetupData->get_focuserdirection() != DirOfTravel)
      {
        mySetupData->set_focuserdirection(DirOfTravel);
        // move is in opposite direction, check for backlash enabled
        // get backlash settings
        if ( DirOfTravel == moving_in)
        {
          if (mySetupData->get_backlash_in_enabled())
          {
            backlash_count = mySetupData->get_backlashsteps_in();
          }
        }
        else
        {
          if (mySetupData->get_backlash_out_enabled())
          {
            backlash_count = mySetupData->get_backlashsteps_out();
          }
        } // if ( DirOfTravel == moving_in)
        /*
                if (DirOfTravel != moving_main && backlash_count)
                {
                  uint32_t sm = mySetupData->get_stepmode();
                  uint32_t bl = backlash_count * sm;
                  DebugPrint("bl: ");
                  DebugPrint(bl);
                  DebugPrint(" ");

                  if (DirOfTravel == moving_out)
                  {
                    backlash_count = bl + sm - ((ftargetPosition + bl) % sm); // Trip to tuning point should be a fullstep position
                  }
                  else
                  {
                    backlash_count = bl + sm + ((ftargetPosition - bl) % sm); // Trip to tuning point should be a fullstep position
                  }

                  DebugPrint("backlash_count: ");
                  DebugPrint(backlash_count);
                  DebugPrint(" ");
                } // if (DirOfTravel != moving_main && backlash_count)
                else
                {
                   Serial.println("false");
                }
        */
      } // if (mySetupData->get_focuserdirection() != DirOfTravel)

      // if target pos > current pos then steps = target pos - current pos
      // if target pos < current pos then steps = current pos - target pos
      steps = (ftargetPosition > driverboard->getposition()) ? ftargetPosition - driverboard->getposition() : driverboard->getposition() - ftargetPosition;

      // Error - cannot combine backlash steps to steps because that alters position
      // Backlash move SHOULD NOT alter focuser position as focuser is not actually moving
      // backlash is taking up the slack in the stepper motor/focuser mechanism, so position is not actually changing
      if ( backlash_count != 0 )
      {
        MainStateMachine = State_Backlash;
      }
      else
      {
        // if target pos > current pos then steps = target pos - current pos
        // if target pos < current pos then steps = current pos - target pos
        driverboard->initmove(DirOfTravel, steps, mySetupData->get_motorSpeed(), mySetupData->get_inoutledstate(), mySetupData->get_reversedirection());
        DebugPrint("Steps: ");
        DebugPrintln(steps);
        MainStateMachine = State_Moving;
      }
      break;
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

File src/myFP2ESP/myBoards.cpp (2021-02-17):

// ---------------------------------------------------------------------------
// TITLE: myFP2ESP DRIVER BOARD CODE
// ---------------------------------------------------------------------------

// ---------------------------------------------------------------------------
// COPYRIGHT
// ---------------------------------------------------------------------------
// (c) Copyright Robert Brown 2014-2021. All Rights Reserved.
// (c) Copyright Holger M, 2019-2021. All Rights Reserved.
// ---------------------------------------------------------------------------

#include <Arduino.h>
#include "generalDefinitions.h"
#include "myBoards.h"

// ____ESP8266 Boards
#if DRVBRD == WEMOSDRV8825H
const char* DRVBRD_ID = "WEMOSDRV8825H";
#elif DRVBRD == WEMOSDRV8825
const char* DRVBRD_ID = "WEMOSDRV8825";
#elif  DRVBRD == PRO2EULN2003
const char* DRVBRD_ID = "PRO2EULN2003";
#elif  DRVBRD == PRO2EDRV8825
const char* DRVBRD_ID = "PRO2EDRV8825";
#elif  DRVBRD == PRO2EL293DNEMA
const char* DRVBRD_ID = "PRO2EL293DNEMA";
#elif  DRVBRD == PRO2EL293D28BYJ48
const char* DRVBRD_ID = "PRO2EL293D28BYJ48";
#elif  DRVBRD == PRO2EL298N
const char* DRVBRD_ID = "PRO2EL298N";
#elif  DRVBRD == PRO2EL293DMINI
const char* DRVBRD_ID = "PRO2EL293DMINI";
#elif  DRVBRD == PRO2EL9110S
const char* DRVBRD_ID = "PRO2EL9110S";

// ____ESP32 Boards
#elif  DRVBRD == PRO2ESP32DRV8825
const char* DRVBRD_ID = "PRO2ESP32DRV8825";

#elif  DRVBRD == PRO2ESP32ULN2003
const char* DRVBRD_ID = "PRO2ESP32ULN2003";
#elif  DRVBRD == PRO2ESP32L298N
const char* DRVBRD_ID = "PRO2ESP32L298N";
#elif  DRVBRD == PRO2ESP32L293DMINI
const char* DRVBRD_ID = "PRO2ESP32L293DMINI";
#elif  DRVBRD == PRO2ESP32L9110S
const char* DRVBRD_ID = "PRO2ESP32L9110S";
#elif  DRVBRD == PRO2ESP32R3WEMOS
const char* DRVBRD_ID = "PRO2ESP32R3WEMOS";
#else
const char* DRVBRD_ID = "UNKNOWN";
#endif

volatile bool timerSemaphore = false;
volatile uint32_t stepcount = 0;
bool stepdir;
byte reverse_dir;
extern DriverBoard* driverboard;
extern bool HPS_alert(void);

// timer Interrupt
#if defined(ESP8266)
#include "ESP8266TimerInterrupt.h"
ESP8266Timer myfp2Timer;                                      // use a unique name for the timer
#else
#include "esp32-hal-cpu.h"                                    // so we can get CPU frequency
hw_timer_t * myfp2timer = NULL;                               // use a unique name for the timer
#endif

/*
  stepcount   HPS_altert    stepdir           action
  ----------------------------------------------------
    0           x             x             stop
    >0        false           x             step
    !0        true        moving_in         stop
    !0        true        moving_out        step
*/

inline void asm2uS()  __attribute__((always_inline));

// On esp8266 with 80mHz clock a nop takes 1/80000000 second, i.e. one clock pulse, or 0.0000000125 of a second
// 2 Microseconds = 2 x 10-6 Seconds or 0.000001
// To get to 2uS for ESP8266 we will need 80 nop instructions
// On esp32 with 240mHz clock a nop takes ? 1/240000000 second or 0.000000004166 of a second
// To get to 2us for ESP32 we will need 240 nop instructions
// TODO
// I need to finish code with clock_frequency and half asm1uS calls if using a clock frequency of 120MHZ on ESP32

inline void asm1uS()                  // 1uS on ESP8266, 1/3uS on ESP32
{
  asm volatile (
    "nop \n\t"
    "nop \n\t"
    "nop \n\t"
    "nop \n\t"
    "nop \n\t"
    "nop \n\t"
    "nop \n\t"
    "nop \n\t"
    "nop \n\t"
    "nop \n\t"
    "nop \n\t"
    "nop \n\t"
    "nop \n\t"
    "nop \n\t"
    "nop \n\t"
    "nop \n\t"
    "nop \n\t"
    "nop \n\t"
    "nop \n\t"
    "nop \n\t"
    "nop \n\t"
    "nop \n\t"
    "nop \n\t"
    "nop \n\t"
    "nop \n\t"
    "nop \n\t"
    "nop \n\t"
    "nop \n\t"
    "nop \n\t"
    "nop \n\t"
    "nop \n\t"
    "nop \n\t"
    "nop \n\t"
    "nop \n\t"
    "nop \n\t"
    "nop \n\t"
    "nop \n\t"
    "nop \n\t"
    "nop \n\t"
    "nop \n\t"
    ::
  );
}

// timer ISR  Interrupt Service Routine
#if defined(ESP8266)
ICACHE_RAM_ATTR void onTimer()
{
  static bool mjob = false;      // motor job is running or not
  if (stepcount  && !(HPS_alert() && stepdir == moving_in))
  {
    driverboard->movemotor(stepdir, true);
    stepcount--;
    mjob = true;                  // mark a running job
  }
  else
  {
    if (mjob == true)
    {
      stepcount = 0;              // just in case HPS_alert was fired up
      mjob = false;               // wait, and do nothing
      timerSemaphore = true;
    }
  }
}
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

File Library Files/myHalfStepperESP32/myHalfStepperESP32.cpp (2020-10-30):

/***********************************************************************************************
* This file is part of the HalfStepper Arduino library.                                        *
* Copyright © 2016 Thomas J. Biuso III  ALL RIGHTS RESERVED...WHATEVER THAT MEANS.             *
* RELEASED UNDER THE LGPL v3.0 LICENSE; SEE <LICENSE> FILE WITHIN DISTRIBUTION ROOT FOR TERMS. *
************************************************************************************************/

#include "myHalfStepperESP32.h"
using namespace HalfStepperOptions;

/* HalfStepper DEFINITION */

// CONSTRUCTORS
HalfStepper::HalfStepper(dword totalSteps, byte pin1, byte pin2, byte pin3, byte pin4,
	SteppingMode steppingMode, PhasingMode phasingMode, SequenceType sequenceType)
	: Stepper(totalSteps, pin1, pin2, pin3, pin4), _PinCount(4), _TotalSteps(totalSteps),
	_SteppingMode(steppingMode), _PhasingMode(phasingMode), _SequenceType(sequenceType)
{
	if (_SteppingMode == SteppingMode::HALF)
		_TotalSteps *= 2;

	_Pins = new byte[_PinCount];

	_Pins[0] = pin1;
	_Pins[1] = pin2;
	_Pins[2] = pin3;
	_Pins[3] = pin4;

	_Stepper = new Stepper(totalSteps, pin1, pin2, pin3, pin4);

	this->UpdateSteps();
}

// DESTRUCTOR
HalfStepper::~HalfStepper()
{
	delete[] _Steps;
	delete _Stepper;
	delete[] _Pins;
}

void HalfStepper::SetSteppingMode(SteppingMode steppingMode)
{
	_SteppingMode = steppingMode;
	this->UpdateSteps();
}

SteppingMode HalfStepper::GetSteppingMode() const { return _SteppingMode; }

void HalfStepper::SetPhasingMode(PhasingMode phasingMode)
{
	_PhasingMode = phasingMode;
	this->UpdateSteps();
}

PhasingMode HalfStepper::GetPhasingMode() const { return _PhasingMode; }

void HalfStepper::SetSequenceType(SequenceType sequenceType)
{
	_SequenceType = sequenceType;
	this->UpdateSteps();
}

SequenceType HalfStepper::GetSequenceType() const { return _SequenceType; }

void HalfStepper::SetDirection(Direction direction) { _Direction = direction; }

Direction HalfStepper::GetDirection() const { return _Direction; }

void HalfStepper::SetPosition(dword position) { _Position = position; }

dword HalfStepper::GetPosition() const { return _Position; }

int HalfStepper::version()
{
	return 69;	// heh...
}

void HalfStepper::step(int numSteps) { this->Step((long)numSteps); }

void HalfStepper::Step(long numSteps)
{
	if (numSteps == 0)
		return;

	if (numSteps > 0)
	{
		_Direction = Direction::FORWARD;
	}
	else
	{
		_Direction = Direction::REVERSE;
		numSteps = abs(numSteps);
	}

	while (numSteps-- > 0)
	{

		if (_Direction == Direction::FORWARD)
		{
			if (_Position++ == _TotalSteps)
				_Position = 0;
		}
		else
		{
			if (_Position-- == 0)
				_Position = _TotalSteps;
		}

		this->DoStep(_Position % (_PinCount * 2));
	}
}

void HalfStepper::StepForward(dword numSteps) { this->Step((long)numSteps); }

void HalfStepper::StepBackward(dword numSteps) { this->Step((long)-1 * (long)numSteps); }

void HalfStepper::StepTo(dword position)
{
	long numSteps = position - _Position;

	if (position >= _TotalSteps)
		position = position % _TotalSteps;

	if (abs(numSteps) > _TotalSteps / 2)
		numSteps = _Position - position;

	this->step(numSteps);
}

// STEP SEQUENCE RETRIEVAL METHOD
void HalfStepper::UpdateSteps()
{
	if (_Steps != NULL)
		delete[] _Steps;

	if (_PinCount == 2)
	{
		_Steps = new byte[4];

		for (int i = 0; i < 4; i++)
			_Steps[i] = pgm_read_byte_near(&_STEP_SEQUENCES_TWO_PIN[BOOL_TO_INDEX((bool)_SteppingMode)][i]);
	}
	else
	{
		_Steps = new byte[8];

		for (int i = 0; i < 8; i++)
		{
			_Steps[i] = pgm_read_byte_near(&_STEP_SEQUENCES_FOUR_PIN[BOOL_TO_INDEX((bool)_SteppingMode)]
				[BOOL_TO_INDEX((bool)_PhasingMode)][BOOL_TO_INDEX((bool)_SequenceType)][i]);
		}
	}
}

// STEP EXECUTION METHOD
void HalfStepper::DoStep(byte stepIdx)
{
	if (_PinCount == 4)
	{
		digitalWrite(_Pins[0], _Steps[stepIdx] & B1000 ? HIGH : LOW);
		digitalWrite(_Pins[1], _Steps[stepIdx] & B0100 ? HIGH : LOW);
		digitalWrite(_Pins[2], _Steps[stepIdx] & B0010 ? HIGH : LOW);
		digitalWrite(_Pins[3], _Steps[stepIdx] & B0001 ? HIGH : LOW);
	}
	else
	{
		digitalWrite(_Pins[0], _Steps[stepIdx] & B0010 ? HIGH : LOW);
		digitalWrite(_Pins[1], _Steps[stepIdx] & B0001 ? HIGH : LOW);
	}
}

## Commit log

2019-08-28 Initial Commit
    Initial upload for myFP2E, common firmware for ESP32/ESP8266
2019-08-28 Library Changes
    Adding zip files for libraries so can be imported into Arduino IDE.
    Fix bug in detection of correct boards in myBoards.h and definitions in myBoards.cpp
    [myBoards.cpp, myBoards.h, myFP2ESP.ino]
2019-08-28 Fixes for board types
    Add conditional defines around some statements to prevent errors on compilation.
    Add myBoardTypes and rearrange loading of .h files to overcome reference issues.
    Move HalfStepper. files into an Arduino Library zip file
    Add OLEDGRAPHICS for Holger to use
    [myBoardTypes.h, myBoards.cpp, myBoards.h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]
2019-08-29 Updates
    Add documentation folder
    Add readme file for Holger re changes
    Move debugging and other def's to generalDefinitions.h file
    Replace Serla. routines in FocuserSetupData.cpp to DebugPrint statements
    [FocuserSetupData.cpp, generalDefinitions.h, myBoardTypes.h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]
2019-08-31 Updates
    recode pushbuttons to active high
    Update schecmatics ESP32
    Add test programs
2019-08-31 Update myFP2ESP.ino
    Add in-out leds to move motor
2019-08-31 Add interrupt code isr to push buttons
    Add test program to handle push buttons on esp32 using isr based code.
2019-08-31 Push Button Fix
    Fix comments re pushbuttons as being active HIGH
2019-09-02 Fixes for Bluetooth
    Bluetooth fixes
    Case 54 fix (no terminator)
    Test program for Bluetooth
    [FocuserSetupData.cpp, L298N-STEP-HALFSTEPPER.ino, generalDefinitions.h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]
2019-09-03 Bluetooth now working
    Fixes for bluetooth, renamed folder
    ESP32 test programs verified
    ESP32 running in AP mode
    [ESP32_RF_INIT.xlsx, ESP8266_RF_init.xls, ESP8266_RF_init.xlsx]
2019-09-04 Add PCB and #D prints etc
    Add schematics, 3D cases/lids, Gerber files for PCB's, updated PDF. Add all files for ESP8266 L293D Motor Shield
    [3D-Case-ESP8266-ULN-L298N-00.stl, 3D-Case-L293D-Shield-00.stl, 3D-Lid-ESP8266-ULN-00.stl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]
2019-09-06 Update myBoards.cpp and Docs
    There was issue with motor jerk on setup() during init of the driver board code. Moving the init of the inputPins[] to before the driver board init appears to be a solution.
    Have also updated docs for hoefully the last time. That is everything from me I think fore release 1. I have changed Version number of firmware to 100,
    [myBoards.cpp, myFP2ESP.ino]
2019-09-16 Conflicts
    DEBUG is conflicting with state of DEBUG in other libraries. Some set it to 0. others set it to 1. have changed to LDEBUG.
    Error in break for case statement in main loop()
    Remove interrupt code for push buttons - does not handle hold down events
    [generalDefinitions.h, myFP2ESP.ino]
2019-09-17 minor fixes and optimizations
    [generalDefinitions.h, myBoardTypes.h, myBoards.cpp]
2019-09-18 Add L293D Motorshield
    Add l293d motorshield
    FIX major errors re board types at compile time - move defines of boardtypes into myBoards,h and use conditional compilation in myBoards.cpp
    [generalDefinitions.h, myBoardTypes.h, myBoards.cpp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]
2019-09-21 Rewrite of Driver Boards
    Major rewrite of DriverBoards
    Remove ChipModels and hardwarePins
    Update documentation
    Some bug fixes
    [FocuserSetupData.cpp, generalDefinitions.h, myBoardTypes.h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]
2019-09-22 ESP32 compile fixes
    Ihad changed some defines in myBoards.h when working on ESP8266 to make them more meaningful. This broke the ESP32 compile. It is now fixed. Aslo delete existing IRREMOTEESP32 library in Arduino libs folder and reload the new one. Also updated the doc/pdf files. And added a 3d printed case.
    [3D-Case-ESP8266-ULN-00.stl]
2019-09-30 Final Changes for BIG CHIP
    Support for BIGCHIP ESP8266 from different supplier which requires D4 instead of SD3 as temperature pin.
    Also some of Holger's code updates.
    [3D-Case-ESP8266-ULN-00.stl, 3D-Case-ESP8266-ULN-L298N-00.stl, 3D-Case-L293D-Shield-00.stl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]
2019-10-02 Add R3WEMOSESP32 board
    Add support for R3 WEMOS ESP32 Dev Board
2019-10-07 OTA and LOCALSERIAL
    Implement OTA nd LocalSerial modes. Add extra files which recently got lost.
    Updated pdf.
    [Bracing for E-oled lid.stl, Case-B-DRV-00.stl, Case-ESP32-DRV-PB-OLED-00.stl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]
2019-10-11 Adafruit Oled
    Fix for Adafruit OLED display
    Fix for pushbuttons and infrared remote and in-out leds incorrect references
    [generalDefinitions.h, myBoards.h, myFP2ESP.ino]
2019-10-11 Fix for Text OLED
    Fix for pin definitions ESP32 and .begin() requirements for ESP82
    [myBoards.h, myFP2ESP.ino]
2019-10-11 Bugfix in backlash mode 2
    [myFP2ESP.ino]
2019-10-12 bugfix i2C pin order and backlash2, minor improvements
    [I2C_scanner.ino, myBoards.h, myFP2ESP.ino]
2019-10-19 Webserver
    Implement webserver
    Move strings to generaldefinitions.h
    Fix drv8825 issues in myboards.cpp
    Update pdf
    [generalDefinitions.h, myBoards.cpp, myBoards.h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]
2019-11-02 Update firmware to v105
    Read firmware change file
    Improve web server
    Fix numerous bugs
    Add ASCOM Remote server
    [Bracing for E-oled lid.stl, Case-B-DRV-00.stl, Case-ESP32-DRV-PB-OLED-00.stl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]
2019-11-23 Fix error in stationmode/accesspoint not connecting
    [myFP2ESP.ino]
2019-12-05 fix minor corrections for v110
    [ascomserver.h, comms.h, myFP2ESP.ino]
2019-12-08 Fix bug in oledgraphics calling readtemp()
    [myFP2ESP.ino]
2019-12-09 Fix feature issue with oled display types
    [myFP2ESP.ino]
2019-12-25 fix issue with mdns server in STATIONMODE
    [generalDefinitions.h, myFP2ESP.ino]
2019-12-25 Fix error in define for OLEDTEXT
    [myFP2ESP.ino]
2019-12-25 fix errors in oled text display
    [generalDefinitions.h, myFP2ESP.ino]
2019-12-26 some minor bug fixes
    [generalDefinitions.h, myBoards.h, myFP2ESP.ino]
2019-12-26 intermediate bugfix config data not complete
    [FocuserSetupData.cpp]
2019-12-26 fixed setupdate_save after 30s
    [FocuserSetupData.cpp, comms.h, myFP2ESP.ino]
2019-12-27 Fix type error in FocuserSetupData.cpp
    [FocuserSetupData.cpp]
2019-12-27 Another type error found.
    [FocuserSetupData.cpp]
2019-12-30 Bug fixes for LOCALSERIAL not compiling
    [comms.h, myFP2ESP.ino]
2019-12-30 Allow BLUETOOTH on WEMOS ESP32 boards
2019-12-30 one merge conflict left and solved
    [myFP2ESP.ino]
2020-01-01 Fix errors in LOCALSERIAL
    [myFP2ESP.ino]
2020-01-05 Fix typo error in Joystick code
    [myFP2ESP.ino]
2020-01-05 Fix IRRemote and Joystick issues, Add TRACE macro
    [FocuserSetupData.cpp, IRREMOTE.ino, generalDefinitions.h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]
2020-01-06 increase size of data_per.jsn doc file and fix coil power release on parked
    [FocuserSetupData.cpp, generalDefinitions.h, myFP2ESP.ino]
2020-01-12 Add reboot button to Management console
    [generalDefinitions.h, myFP2ESP.ino]
2020-01-20 r117 update, add READWIFICONFIG and bug fixes
    [FocuserSetupData.cpp, comms.h, generalDefinitions.h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]
2020-01-24 Add support for OLED 1.3inch displays using SSH1306 driver chip
2020-01-24 Add check for oled driver type, add to oledgraphic
2020-01-24 Fix oled not working on WEMOSESP32 board
    [myBoards.h]
2020-03-26 rework on myBoards.cpp, new display.cpp
    [FocuserSetupData.cpp, comms.h, displays.cpp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]
2020-04-20 moving motor with timer interrupt
2020-05-13 update timer isr, home position sensor, halt command
2020-05-19 Fix errors in HPSW code
    [myFP2ESP.ino]
2020-06-08 fixed bug in timerSemaphore
    [FocuserSetupData.cpp, displays.cpp, myBoards.cpp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]
2020-07-28 remove all references to driverboard->get/set/motorspeed
2020-07-29 v121 updates
    [Compile Sizes.xlsx]
2020-07-29 add /rebootxx to management server
    [generalDefinitions.cpp, generalDefinitions.h, myFP2ESP.ino]
2020-07-30 fix for interrupt causing crash on long moves
    [generalDefinitions.h, myBoards.cpp, myBoards.h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]
2020-07-30 fix for uln2003 and other issues
    [Compile Sizes.xlsx]
2020-07-30 adjust for clock rate of ESP32 when moving motor
2020-08-08 126 massive update
    [Compile Sizes.xlsx]
2020-08-08 add correction for uln2003 driver board
    [myBoards.h]
2020-08-10 Fix for targetposition being set to 0 on startup
    [myBoards.cpp, myBoards.h, myFP2ESP.ino]
2020-08-10 fix for rebooting linked to focusersetupdata.cpp
    [FocuserSetupData.cpp]
2020-08-22 Fix for get temperature
    [comms.h, myFP2ESP.ino]
2020-09-04 Fix errors in currentposition
    [displays.cpp, myFP2ESP.ino]
2020-09-04 fix updating of focuser position
    [myFP2ESP.ino]
2020-09-05 Changes to HalfStepperESP32 library and other fixes
    [FocuserSetupData.cpp, displays.cpp, generalDefinitions.cpp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]
2020-09-05 Fix dangling reference in myboards.h
    [generalDefinitions.cpp, myBoards.h, myFP2ESP.ino]
2020-09-06 add temp xhtml to webserver and update stepper routines
2020-09-06 hpsw fixes, ascom root page fixes
    [Compile Sizes.xlsx]
2020-09-12 all driver boards tested
2020-09-15 Fix for L293D shield myFP2EL293D28BYJ48 motor not reversing
    [FocuserSetupData.cpp, myFP2ESP.ino]
2020-10-17 bug fix OLED_TEXT inverted
    [displays.cpp]
2020-10-17 quick relocation of temperature probe to temp.cpp
2020-10-18 put all Temperature Probe stuff in a class in temp.cpp and temp.h
2020-12-16 Update myBoards.cpp
    Incorrect spelling for PRO2ESP ULN2003 and L298N boards - was PRO2EE
2020-12-17 Update ManagementServer.cpp
    Fix for mDNS service not being able to stop or start
    [ManagementServer.cpp]
2020-12-29 New test programs for home position switch
2021-01-01 Update myFP2ESP.ino
    apply fix for fcurrentposition compile issue within IR code
    [myFP2ESP.ino]
2021-01-02 Update myFP2ESP.ino
    Fix for reverse direction
    Fix for esp8266 compile error
    [myFP2ESP.ino]
2021-01-02 Update myBoards.cpp
    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
    [myBoards.cpp]
2021-01-02 Update webserver.cpp
    Fixes to match updates to webpage
    [webserver.cpp]
2021-01-02 Update generalDefinitions.h
    Update to definitions for management server: backlash steps in and out buttons
    [generalDefinitions.h]
2021-01-02 Update msindex3.html
    Update to include backlash steps buttons
2021-01-02 Update generalDefinitions.h
    Fix for 'MINOLEDPAGETIME' was not declared in this scope
    [generalDefinitions.h]
2021-01-02 Update ManagementServer.cpp
    Fix for init_temp() error
    [ManagementServer.cpp]
2021-01-02 Update comms.h
    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
    [comms.h]
2021-01-02 Update ManagementServer.cpp
    Fix for OLEDTEXT to OLED_TEXT
    [ManagementServer.cpp]
2021-01-02 Update comms.h
    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
    [comms.h]
2021-01-02 Update generalDefinitions.h
    Remove redundant defines for OLED
    #define OLED_ADDR 0x3C // some OLED displays maybe at 0x3F, use I2Cscanner to find correct address
    #define SCREEN_WIDTH 128 // OLED display width, in pixels
    #define SCREEN_HEIGHT 64 // OLED display height, in pixels
    [generalDefinitions.h]
2021-01-02 Update webserver.cpp
    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
    [webserver.cpp]
2021-01-02 Update myFP2ESP.ino
    Remove DEBUG errors in readwificonfig()
    [myFP2ESP.ino]
2021-01-02 Update myFP2ESP.ino
    Add halt to IRRemote
    Clean up software reboot()
    [myFP2ESP.ino]
2021-01-02 Update ManagementServer.cpp
    Error in include
    [ManagementServer.cpp]
2021-01-03 Update ManagementServer.cpp
    Fix for OLED_TEXT
    [ManagementServer.cpp]
2021-01-03 Update webserver.cpp
    Fix for OLED_TEXT and OLED_MODE
    [webserver.cpp]
2021-01-03 Update generalDefinitions.cpp
    Fix for ! not showing on OLED displays
    [generalDefinitions.cpp]
2021-01-03 Update myFP2ESP.ino
    Fix for HPSW
    [myFP2ESP.ino]
2021-01-03 Update generalDefinitions.h
    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
    [generalDefinitions.h]
2021-01-03 Update myBoards.cpp
    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
    [myBoards.cpp]
2021-01-05 Update myFP2ESP.ino
    Fix for controller continually rebooting when webserver or ascomserver is enabled then controller rebooted
    [myFP2ESP.ino]
2021-01-05 Update webserver.cpp
    Fix for controller continually rebooting when webserver or ascomserver is enabled and then controller is rebooted
    [webserver.cpp]
2021-01-05 Update Ascom.cpp
    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
    [Ascom.cpp]
2021-01-12 Update webserver.cpp
    Fix for WEBSERVER_handletemperature not found
    [webserver.cpp]
2021-01-29 Add new options to comms.h
    Add extra calls to support new features
    Make compatible with myFocuserPro2 applications
    Make compatible with myFocuserPro2 INDI driver
2021-01-29 Change to focuserconfig.h to support INDI
    Change focuserconfig,h to allow INDI usage by either TCP/IP or Serial, using the myFocuserPro2 INDI driver.
2021-02-06 Update webserver.cpp
    Missing statement which indicates webserver is now running
    [webserver.cpp]
2021-02-08 Update myFP2ESP.ino
    Add optional fallback SSID and PASSWORD
    Recode Backlash
    [myFP2ESP.ino]
2021-02-08 Update generalDefinitions.h
    Add backlash state
    [generalDefinitions.h]
2021-02-08 Update webserver.cpp
    Webserver running fix
    [webserver.cpp]
2021-02-11 Update FocuserSetupData.h
    add motorspeeddelay to support change via management server
2021-02-11 Update FocuserSetupData.cpp
    Add motorspeeddelay support code
2021-02-11 Update myFP2ESP.ino
    Add support for motorspeeddelay config
2021-02-11 Update msindex3.html
    Add support for motor speed delay setting
2021-02-11 Update ManagementServer.cpp
    Fix for isMoving reference not found
    Fix for init_temp error
    Fix for driverboard not found
    Fix for halt_alert not found
    Fix for ftargetPosition not found
    [ManagementServer.cpp]
2021-02-11 Update ManagementServer.cpp
    Add code to handle motor speed delay
2021-02-11 Add backlash state
2021-02-11 All the fixes combined - see firmware changes text file
    [comms.h, myFP2ESP.ino, webserver.cpp]
2021-02-14 Merged branch 135 into master and address compilation errors
    [ManagementServer.cpp, myBoards.h, myFP2ESP.ino]
2021-02-14 Change stepmode to int type - set groundwork for supporting Trimac drivers in future
2021-02-15 Fix for second network credentials
    [myFP2ESP.ino, webserver.cpp]
2021-02-15 Fix for HPSW not working when backlash enabled
    [generalDefinitions.cpp, myBoards.cpp, myBoards.h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]
2021-02-16 Fix for home position switch - hcomet
    [myFP2ESP.ino]
2021-02-16 Fix reboot of controller when enable tempprobe
    [Ascom.cpp, FocuserSetupData.cpp, ManagementServer.cpp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]
2021-02-16 Fix for RSSI to update on each request
    [ManagementServer.cpp, comms.h, generalDefinitions.cpp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]
2021-02-17 Fix for warnings and compiler error
    [Compile Sizes.xlsx]
2021-02-20 fix for compiler error on some boards
    [myBoards.h]
